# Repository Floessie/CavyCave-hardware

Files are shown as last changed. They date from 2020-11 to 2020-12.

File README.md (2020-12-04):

# CavyCave (hardware)

[][cc-by-sa]

## About

*CavyCave* is a temperature controlled box for guinea pigs and other small animals kept outside in winter. This repository holds the KiCad files for the controller board.

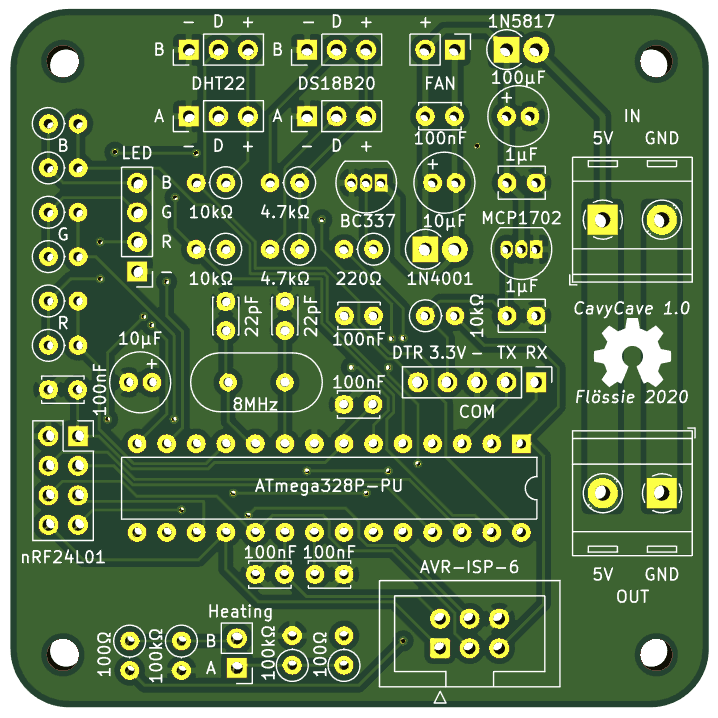
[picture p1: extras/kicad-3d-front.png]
KiCad 3D view


### The box

The box is built around a dark floor tile on a base frame of battens. Walls and top cover are made of 17&nbsp;mm thick, glued spruce floorboards. The front wall is fixed with four latches and can be removed for cleaning the interior. A number of load resistors fixed with thermal glue underneath the tile provide comfortable warmth to the top, helped by a polyurethane panel, which is clamped into the base frame at the bottom.

A hole in the top right corner of the box serves together with a fan as the exhaust air outlet. To protect the cavies from inspecting the fan too closely, a two-walled plywood housing is glued onto the backside of the box corner.

Two sensors monitor the temperature and humidity: a DHT22 for air temperature and humidity located in the top right corner of the box near the fan, and a cased DS18B20 under the tile for the floor temperature.

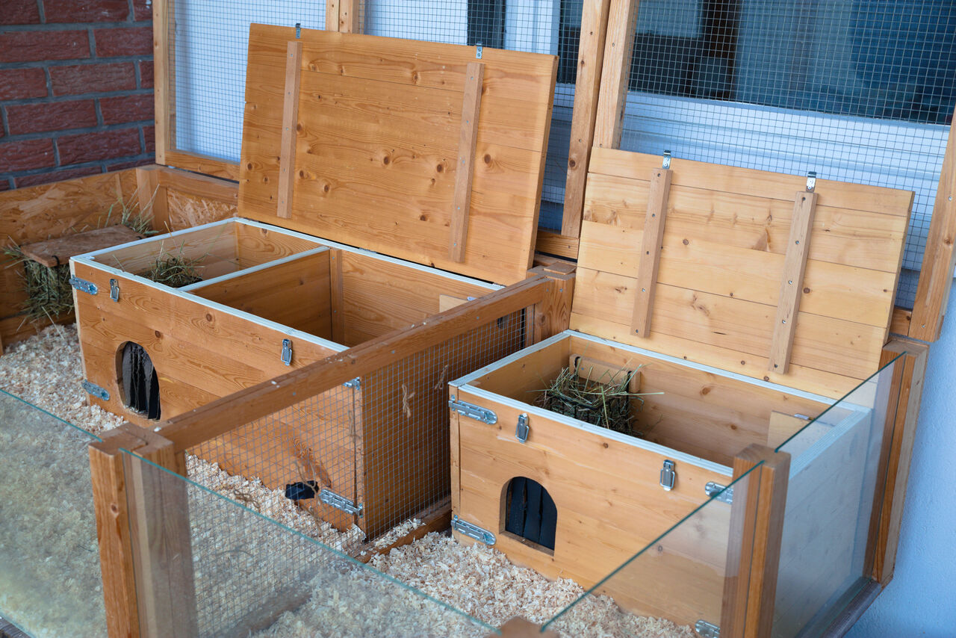
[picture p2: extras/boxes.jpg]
The boxes
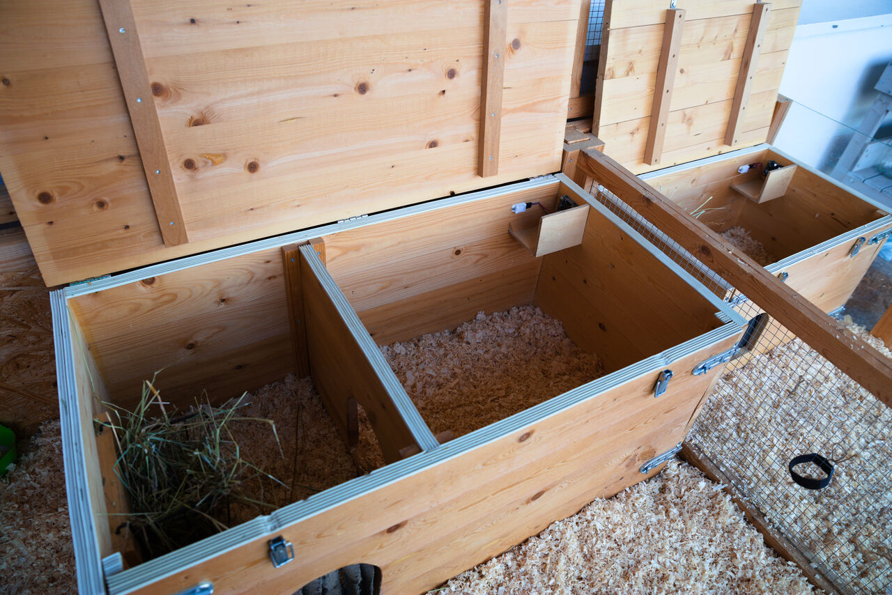
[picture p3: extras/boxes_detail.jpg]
Details
                       | 
-----------------------------------------------------|-------------------------------------------------
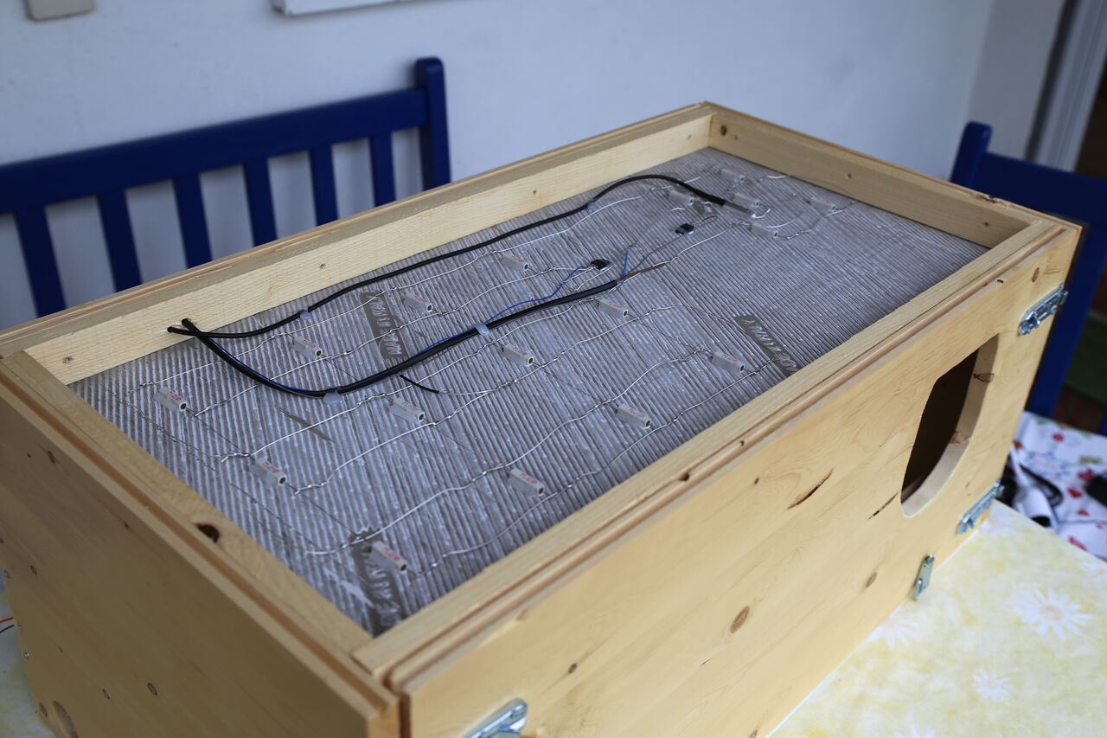
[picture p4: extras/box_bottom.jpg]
Load resistors and MOSFETs
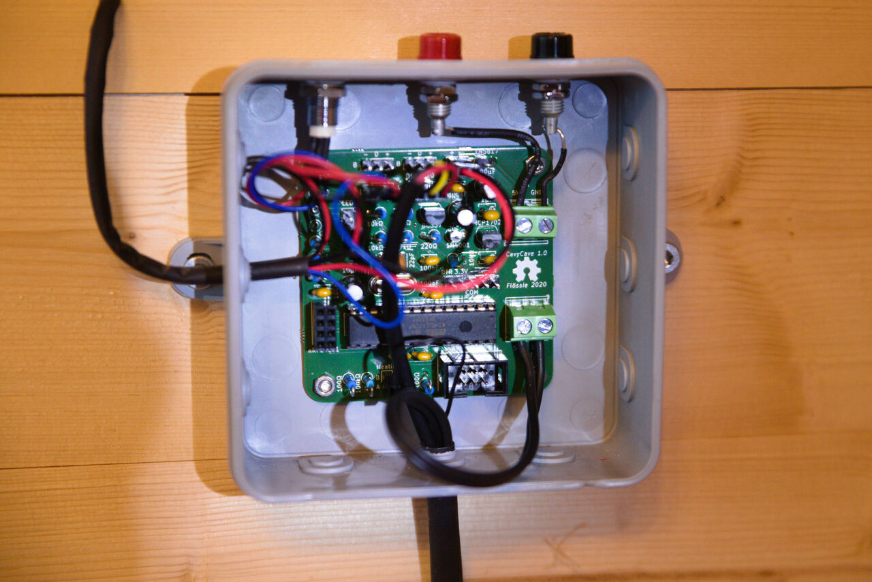
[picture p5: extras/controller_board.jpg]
Controller board
 | 

### The controller board

The heart and brain of the controller board is an ATmega328P-PU as found on the popular Arduino boards. Internally supplied with 3.3&nbsp;volts it connects two DHT22 temperature and humdity sensors and two DS18B20 temperature sensors as input and drives two heating circuits and one fan. The input voltage for the board, the fan, and the heating is 5&nbsp;volts. Depending on the load resistors the heating power is about 15 to 20&nbsp;watts.

The control system can be monitored, configured and remotely controlled by an nRF24L01+.

#### BOM

Quantity | Part | Mandatory
---------|------|----------
1 | Diode 1N5817 | :heavy_check_mark:
1 | Diode 1N4001 | :heavy_check_mark:
2 | Capacitor 22pF |
5 | Capacitor 100nF | :heavy_check_mark:
1 | Capacitor 100nF |
2 | Capacitor 1µF | :heavy_check_mark:
1 | Capacitor 10µF | :heavy_check_mark:
1 | Capacitor 10µF |
1 | Capacitor 100µF | :heavy_check_mark:
1 | Resistor 100Ω | :heavy_check_mark:
1 | Resistor 100Ω |
1 | Resistor 220Ω | :heavy_check_mark:
1 | Resistor 4.7kΩ | :heavy_check_mark:
1 | Resistor 4.7kΩ |
2 | Resistor 10kΩ | :heavy_check_mark:
1 | Resistor 10kΩ |
1 | Resistor 100kΩ | :heavy_check_mark:
1 | Resistor 100kΩ |
1-6 | Resistor for LED | :heavy_check_mark:
12-18 | Load resistor 22Ω VitrOhm KH208-810B22R | :heavy_check_mark:
2m+ | Silver plated copper wire 0.8mm | :heavy_check_mark:
1 | Bicolor (3 pin, CC) or RGB (4 pin, CC) LED | :heavy_check_mark:
1 | Transistor BC337-40 | :heavy_check_mark:
1 | LDO regulator MCP1702-3002 | :heavy_check_mark:
2 | Terminal block RND 205-00232 | :heavy_check_mark:
1 | Black 4mm socket Hirschmann 930 176-100 |
1 | Red 4mm socket Hirschmann 930 176-101 |
1 | MOSFET IRLIZ34N | :heavy_check_mark:
1 | MOSFET IRLIZ34N |
1 | Sensor DHT22 | :heavy_check_mark:
1 | Sensor DHT22 |
1 | Sensor DS18B20 | :heavy_check_mark:
1 | Sensor DS18B20 |
1 | Fan Sunon MB40100V2-000U-A99 | :heavy_check_mark:
1 | Crystal HC49U 8MHz |
1 | Pin socket 2x4 |
1 | IDC header 2x3 |
1 | Radio module nRF24L01+ |
x | Single row pin headers | :heavy_check_mark:

### History

This project started in the fall of 2018 with a large box for four cavies and two "rooms" ("vestibule" and "lounge") seperately heated. When one cavy was pushed out of the group in summer 2019 another smaller box had to be built, which has only one heating circuit. For the first box I experimented with 9V input to get 30&nbsp;watts heating power, but that was too much for the polyurethane panel and resulted in hot spots over the load resistors. Still, this could be a solution for even larger boxes with more and higher resistive load resistors as it's easier to find high power 9V supplies than 5V supplies. The fan must then be adjusted accordingly. The MCP1702-3002 LDO regulator for the internal 3.3&nbsp;volts supports up to 13.2&nbsp;volts input operating voltage.

The prototype circuit proved itself two winters, so now it was time to convert it to a real PCB.

## License

This work is licensed under a
[Creative Commons Attribution-ShareAlike 4.0 International License][cc-by-sa].

[][cc-by-sa]

[cc-by-sa]: http://creativecommons.org/licenses/by-sa/4.0/
[cc-by-sa-image]: https://licensebuttons.net/l/by-sa/4.0/88x31.png
[cc-by-sa-shield]: https://img.shields.io/badge/License-CC%20BY--SA%204.0-lightgrey.svg

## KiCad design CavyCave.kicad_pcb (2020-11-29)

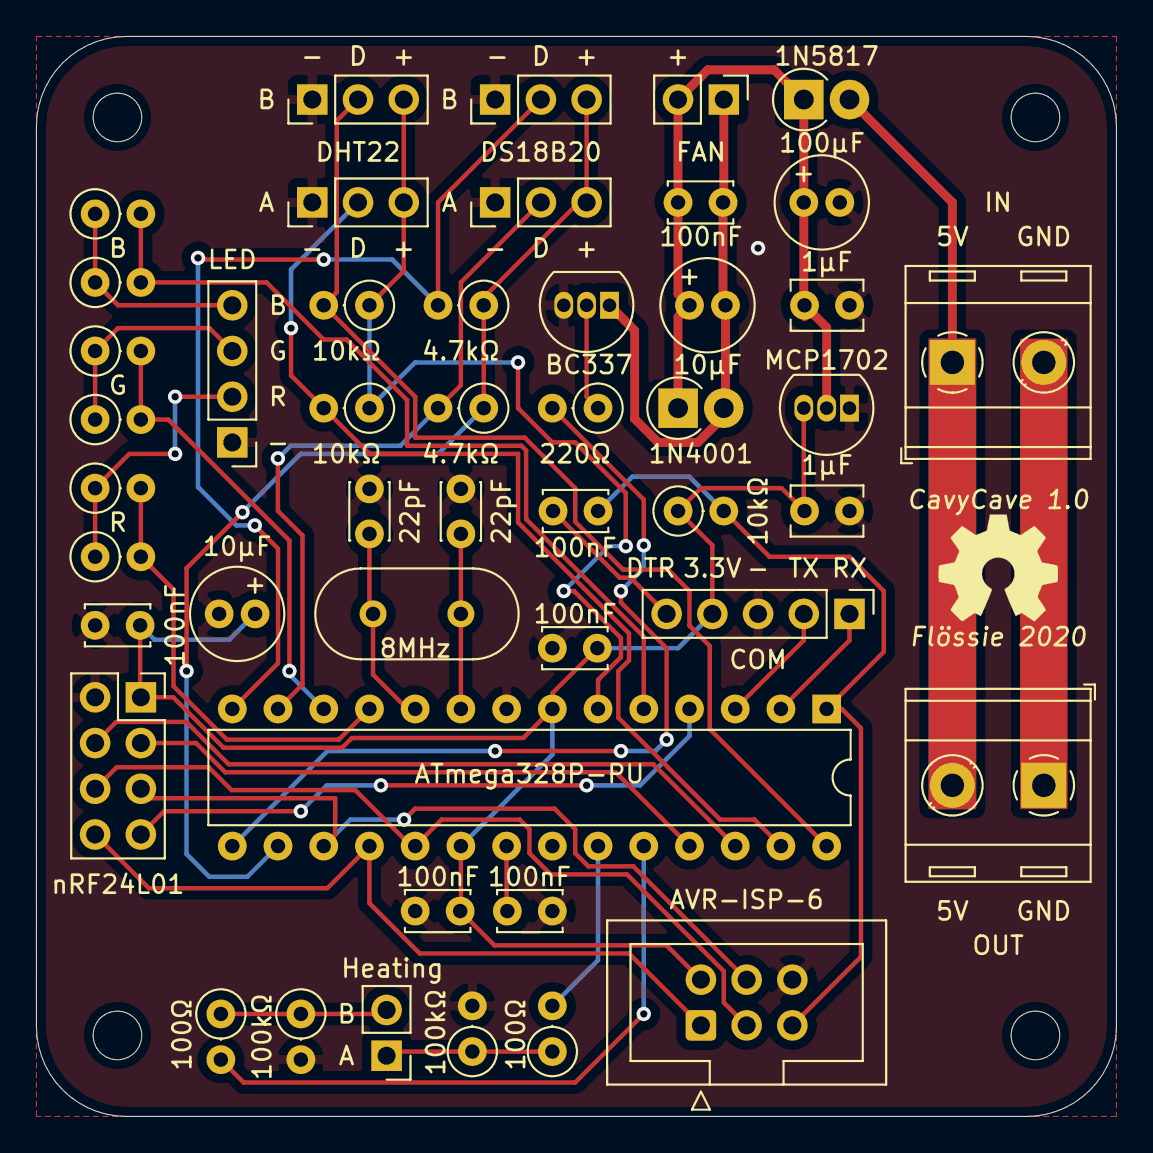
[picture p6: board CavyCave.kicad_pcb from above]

Board: 2 copper layers, 60.0 x 60.0 mm, 47 parts (0 on the bottom side), 36 nets.

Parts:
B: R; R_Axial_DIN0207_L6.3mm_D2.5mm_P2.54mm_Vertical
C1, C2: 1µF; C_Disc_D3.8mm_W2.6mm_P2.50mm
C3: 100µF; C_Radial_D5.0mm_H11.0mm_P2.00mm
C4, C6, C7, C10, C12, C13: 100nF; C_Disc_D3.4mm_W2.1mm_P2.50mm
C5, C11: 10µF; C_Radial_D5.0mm_H11.0mm_P2.00mm
C8, C9: 22pF; C_Disc_D3.0mm_W2.0mm_P2.50mm
D1: 1N5817; D_DO-41_SOD81_P2.54mm_Vertical_AnodeUp
D2: 1N4001; D_DO-41_SOD81_P2.54mm_Vertical_AnodeUp
G: R; R_Axial_DIN0207_L6.3mm_D2.5mm_P2.54mm_Vertical
J1: IN; TerminalBlock_RND_205-00287_1x02_P5.08mm_Horizontal
J2: OUT; TerminalBlock_RND_205-00287_1x02_P5.08mm_Horizontal
J3: FAN; PinHeader_1x02_P2.54mm_Vertical
J4: LED; PinHeader_1x04_P2.54mm_Vertical
J5: Heating; PinHeader_1x02_P2.54mm_Vertical
J6: COM; PinHeader_1x05_P2.54mm_Vertical
J7: DHT22 A; PinHeader_1x03_P2.54mm_Vertical
J8: DHT22 B; PinHeader_1x03_P2.54mm_Vertical
J9: nRF24L01; PinSocket_2x04_P2.54mm_Vertical
J10: AVR-ISP-6; IDC-Header_2x03_P2.54mm_Vertical
J11: DS18B20 A; PinHeader_1x03_P2.54mm_Vertical
J12: DS18B20 B; PinHeader_1x03_P2.54mm_Vertical
Q1: BC337; TO-92_Inline
R, R4, R6, R8: R; R_Axial_DIN0207_L6.3mm_D2.5mm_P2.54mm_Vertical
R1: 220Ω; R_Axial_DIN0207_L6.3mm_D2.5mm_P2.54mm_Vertical
R2, R13, R14: 10kΩ; R_Axial_DIN0207_L6.3mm_D2.5mm_P2.54mm_Vertical
R9, R11: 100Ω; R_Axial_DIN0207_L6.3mm_D2.5mm_P2.54mm_Vertical
R10, R12: 100kΩ; R_Axial_DIN0207_L6.3mm_D2.5mm_P2.54mm_Vertical
R15, R16: 4.7kΩ; R_Axial_DIN0207_L6.3mm_D2.5mm_P2.54mm_Vertical
U1: MCP1700-3302; TO-92_Inline
U2: ATmega328P-PU; DIP-28_W7.62mm
Y1: 8MHz; Crystal_HC49-U_Vertical

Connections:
+3V3: C1.2, C4.2, C6.2, C11.1, C12.2, J6.4, J9.1, J10.2, R2.1, U1.3, U2.7, U2.20
/5V: C2.2, C3.1, C5.1, C7.1, D1.1, D2.1, J3.2, U1.2
/B: B.2, R8.2, U2.5
/CE: J9.4, U2.26
/CSN: J9.3, U2.25
/DHT_A: J7.2, R13.2, U2.27
/DHT_B: J8.2, R14.2, U2.28
/DHT_PWR: J7.3, J8.3, R13.1, R14.1, U2.6
/DS_A: J11.2, R15.2, U2.13
/DS_B: J12.2, R16.2, U2.14
/DS_PWR: J11.3, J12.3, R15.1, R16.1, U2.16
/FAN: R1.2, U2.15
/G: G.2, R6.2, U2.12
/HEAT_A: R9.2, U2.23
/HEAT_B: R11.2, U2.24
/IRQ: J9.7, U2.4
/MISO: J9.8, J10.1, U2.18
/MOSI: J9.5, J10.4, U2.17
/R: R.2, R4.2, U2.11
/RST: C10.1, J10.5, R2.2, U2.1
/RX: J6.1, U2.2
/SCK: J9.6, J10.3, U2.19
/TX: J6.2, U2.3
GND: C1.1, C2.1, C3.2, C4.1, C6.1, C8.2, C9.2, C11.2, C12.1, C13.1, J1.2, J2.1, J4.1, J6.3, J7.1, J8.1, J9.2, J10.6, J11.1, J12.1, Q1.3, R10.2, R12.2, U1.1, U2.8, U2.22
unnamed: C5.2, C7.2, D2.2, J3.1, Q1.1
unnamed: C8.1, U2.10, Y1.2
unnamed: C9.1, U2.9, Y1.1
unnamed: C10.2, J6.5
unnamed: C13.2, U2.21
unnamed: D1.2, J1.1, J2.2
unnamed: J4.2, R.1, R4.1
unnamed: G.1, J4.3, R6.1
unnamed: B.1, J4.4, R8.1
unnamed: J5.1, R9.1, R10.1
unnamed: J5.2, R11.1, R12.1
unnamed: Q1.2, R1.1

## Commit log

2020-11-29 Add v1.0 KiCad files, license, and minimal README
    [CavyCave.kicad_pcb, CavyCave.sch]
2020-12-01 Roughly describe the box and the controller board
2020-12-01 Add BOM
2020-12-01 Add LED to BOM
2020-12-02 Add load resistors and wire to BOM
2020-12-04 Add input sockets

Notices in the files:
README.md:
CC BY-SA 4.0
